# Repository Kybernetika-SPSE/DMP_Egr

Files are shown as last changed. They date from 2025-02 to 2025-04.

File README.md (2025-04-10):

# Stanice pro monitorování okolního prostředí

## Zadání
Cílem práce je navrhnout a vytvořit model pásové linky, která bude využívat robotickou ruku na manipulaci se zásilkami.

## Vedoucí práce
Jiří Švihla

## Harmonogram práce
- [x]   Návrh celého modelu a výběr potřebných součástek (31.10.)
- [x]   Návrh a vytvoření jednotlivých pásů (28.11.)
- [x]   Seznámení se s fungování robotického ramena (19.12.)
- [x]   Vývoj softwaru pro řízení celého modelu (30.1.)
- [x]   Kompletování modelu a následné testovaní (27.2.)
- [x]   Zpracování dokumentace (24. 3.)

## Termín odevzdání
31. března 2025

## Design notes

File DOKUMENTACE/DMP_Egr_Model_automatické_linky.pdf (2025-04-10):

## Vyšší odborná škola

## a Střední průmyslová škola elektrotechnická

## Plzeň, Koterovská 85

DLOUHODOBA MATURITN ´ | Í PRACE ´

## S OBHAJOBOU

### Téma:

# Model automatické linky

Autor práce: | Lukáš Egr
Třída: | 4.L

## Vedoucí práce: Jiří Svihla ˇ

Dne: | 31.3.2025

## Hodnocení:

Vyšší odborná škola
a Střední průmyslová škola elektrotechnická Plzeň, Koterovská 85

# Zadání dlouhodobé maturitní práce

Žák: | Lukáš EGR
Třída: | 4. L

### Studijní obor: 78-42-M/01 Technické lyceum

Zaměření: | bez zaměření
Školní rok: | 2024 - 2025
Téma práce: | Model automatické linky

### Pokyny k obsahu a rozsahu práce:

Cílem práce je navrhnout a vytvořit model pásové linky, která bude využívat robotickou ruku na manipulaci se zásilkami.

1. Návrh celého modelu a výběr potřebných součástek (31.10.) 2. Návrh a vytvoření jednotlivých pásů (28.11.) 3. Seznámení se s fungování robotického ramena (19.12.) 4. Vývoj softwaru pro řízení celého modelu (30.1.) 5. Kompletování modelu a následné testovaní (27.2.) 6. Zpracování dokumentace (24.3.)

Termín odevzdání: | 31. března 2025
Čas obhajoby: | 15 minut
Vedoucí práce: | Jiří Švihla

Projednáno v katedře ODP, a schváleno ředitelem školy.

V Plzni dne: 30. září 2024 | Mgr. Jan Syřínek Zástupce ŘŠ , zástupce statutárního orgánu Vedoucí organizace VOŠ, SŠ, DM

## Anotace

Tato maturitní práce se zabývá návrhem a sestavení modelu automatické třídicí linky,

která simuluje proces třídění příchozích výrobků. Linka se skládá z pásového dopravníku

a robotického ramene, které se stará o manipulaci s výrobky a jejich následné třídění do

určených pozic.

Cílem projektu je vytvořit funkční systém, který umožní automatické rozpoznávání a

třídění výrobků podle definovaných pravidel. Díky tomu můžeme nahlédnout do světa

průmyslové automatizace a její složitosti.

Prohlašuji, že jsem tuto práci vypracoval samostatně a použil literárních pramenů

a informací, které cituji a uvádím v seznamu použité literatury a zdrojů informací.

Prohlašuji, že jsem nástroje UI využil v souladu s principy akademické integrity a že na

využití těchto nástrojů v práci vhodným způsobem odkazuji.

Souhlasím s využitím mé práce učiteli VOS a SP ˇ | SE Plzeň k výuce. ˇ
V Plzni dne 31. 3. 2025 | Podpis: |

## Annotation

This graduation thesis deals with the design and implementation of a model of an auto-

matic sorting line that simulates the process of sorting of incoming products. The line is

composed of a conveyor belt, and a robotic arm that takes care of the manipulation of

products and their subsequent sorting into certain positions.

The aim of the project is to create a functional system that allows automatic recognition

and sorting of products according to defined rules. This will give us an insight into the

world of industrial automation and its complexity.

I declare that I have prepared this thesis independently and have used literature sour-

ces and information, which I cite and list in the list of used literature and sources of

information.

I declare that I have used the UI tools in accordance with the principles of academic

integrity and that I have appropriately referenced the use of these tools in my work.

I agree to the use of my work by the teachers of the Higher School of Education and

Secondary School of Education Pilsen for teaching.

In Pilsen 31. 3. 2025 | Podpis: |

## Obsah

Uvod ´ | 6
1 Hardware | 7
2 Software | 15
3 Závěr | 19
Literatura | 20
Přílohy | 22

## Uvod ´

V dnešní době se stále více firem spoléhá na automatizaci, která jim umožňuje zvýšit

efektivitu a přesnost logistických procesů. Se zvyšujícím se objemem online objednávek

roste i tlak na co nejrychlejší a nejspolehlivější třídění a doručování zásilek.

Automatizované systémy třídění se proto využívají nejen v logistice, ale také v průmyslové

výrobě, kde je potřeba efektivně rozřazovat produkty podle různých kritérií, například

podle barvy, hmotnosti nebo rozměrů. Klíčovou součástí těchto systémů jsou dopravníky,

senzory a robotická ramena, která umožňují manipulaci s objekty a jejich přesné umístění

na požadovaná místa.

### Cíl práce

Cílem této práce je navrhnout a realizovat model automatické třídicí linky, která demon-

struje principy moderních třídicích systémů. Linka bude využívat dopravní pás, senzo-

rický systém a robotickou ruku k rozřazování objektů představujících balíčky či výstupy

z výroby. V rámci projektu bylo nutné nejen navrhnout a sestavit mechanickou konstrukci

linky, ale také vyvinout odpovídající software, který zajistí její správné fungování – od

inicializace, přes detekci objektů, až po jejich přesné umístění do předem definovaných

pozic.

Tento projekt ukazuje, jak lze pomocí kombinace mechanických a elektronických prvků

spolu s programovým řízením vytvořit efektivní třídicí systém, který může sloužit jako

základ pro větší a komplexnější automatizační řešení.

6

## 1 Hardware

Pro realizaci automatické třídicí linky bylo nutné navrhnout a sestavit jednotlivé hardwa-

rové komponenty tak, aby společně tvořily funkční celek. Každá část linky plní specific-

kou úlohu a simuluje tím reálný automatický systém, který dokáže pracovat bez nutnosti

uživatelského zásahu. Klíčovými prvky jsou robotické rameno, které manipuluje s objekty, dopravníkový pás, zajišt’ující jejich přesun a identifikaci, a napájecí systém dodávající

energii všem komponentám.

### 1.1 Rameno

Robotické ramena ruky jsou obvykle, jako i v mém případě, poháněna servomotory, které umožňují přesný a rychlý pohyb. Rídicí signál, který servo přijímá, je často ve formě délky ˇ

impulzu neboli PWM (Pulse Width Modulation). Elektronická deska serva tento signál

přijme a poté měří šířku daného impulsu v čase, která určuje požadovanou polohu motoru (viz. Obrázek 1.1). Motor pak reaguje na tento signál otáčením do určitého úhlu, který

se servo snaží udržet nepřetržitou korekcí polohy [1]. Tímto způsobem lze servo motory

napozicovat podle potřeb do předem definovaných pozic.

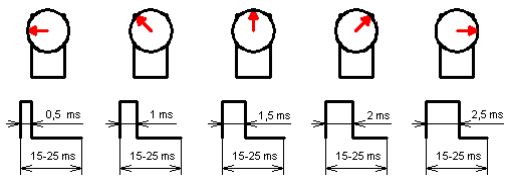
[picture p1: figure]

Obrázek 1.1: Příklady PWM signálu [2]

7

Robotická ruka je vybavena šesti servomotory MG996R, které umožňují pohyb v rozsahu

120 stupňů, tedy 60 stupňů na každou stranu. Tento rozsah otáčení poskytuje dostatečnou

flexibilitu pro manipulaci s objekty v pracovním prostoru ramene. Maximální dosah ruky

činí až 35 cm, což je pro model více něž dostačující.

Základna robotické ruky je konstruována z dvou hliníkových profilů, které zajišt’ují stabilní

uchycení celé konstrukce ramena. Tyto profily jsou upevněny na desku pomocí několika

úhelníků, šroubů M8 a závrtných matic. Díky tomu je garantována vysoká stabilita ro-

botického ramene, což je klíčové pro jeho přesné a spolehlivé fungování.

### 1.2 Dopravníkový pás

Dopravníkový pás je jedna z hlavních prvků modelu třídicí linky, je složen z 3D tištěných

dílů, ložisek, hlazených tyčí, gumového pásu a hliníkových profilů. Právě použití těchto

dílů umožňuje variabilní sestavení pásu. Například je možné veškeré díly jednoduše z kon-

strukce pásu demontovat nebo je naopak na konstrukci přidat.

Díky 3D tisku jsem mohl veškeré modely přizpůsobit pro potřeby jednotlivých komponent

a potřeb celého modelu. Byla brána v potaz, jak velikost součástek, tak i jejich umístění,

myslelo se ale i na množství spotřebovaného materiálu nebo cirkulaci vzduchu, abych

zamezil přehřívání součástek. Veškeré díly jsou do hliníkových profilů umístěny pomocí

šroubů M6 s válcovou hlavou a zajištěny příslušnou maticí.

### Konstrukce dopravníku

Hlavní konstrukce dopravníku je tvořena čtyřmi hliníkovými profily různých délek. Spe-

cificky mají rozměry 30 na 30 mm a délku 400 mm a 40 mm a navzájem jsou spojeny tzv. úhelníky (viz. Obrázek 1.2). Střed konstrukce dopravníkového pásu je vyztužena několika žebry, které zajišt’ují celkovou pevnost celého pásu a zároveň zabraňují prověšení

pásu ve ve středu mezi profily (Přílohy I a II).

Nohy dopravníkového pásu jsou také 3D tištěné (Příloha III). Model jako takový je

8

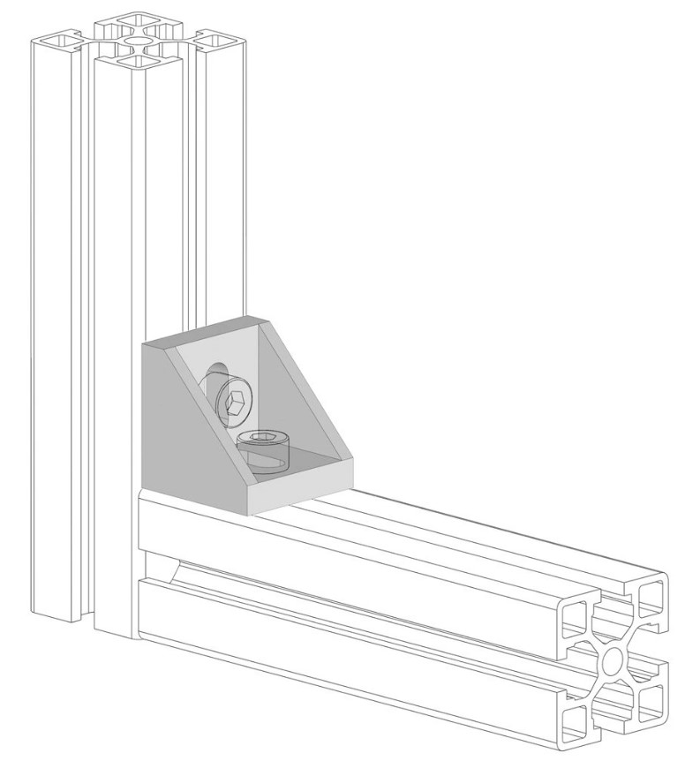
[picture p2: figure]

Obrázek 1.2: Nastínění spojení profilů [3]

navržen tak, aby přesahoval o 2 mm nad plochu profilů. To napomáhá plynulému chodu

gumového pásu, kterému přesah slouží jako ”kolejnice”, do kterých pás plynule zajede.

Zabraňují tedy ve vyklouzávání gumového pásu a udržuje ho ve správné poloze.

### Krokový motor

Gumový pás je poháněn díky krokovému motoru NEMMA 17, který disponuje silou 40 N · cm. Motor je na konstrukci dopravníku upevněn díky tištěnému 3D modelu

(Příloha IV ) a abych co nejvíce eliminoval vibrace, spojené s pohybem motoru, je mezi

model a motor vložena gumová vložka.

Z důvodu velikosti a váze motoru je motor umístěn pod samotným dopravníkem. Točivý

moment motoru je na hlazenou tyč poté převáděn pomocí převodu složeného ze dvou

řemeniček a řemenu.

Abych zvětšil poloměr otáčení, je na hlazené tyči umístěn tištěný válec (Příloha V ). Tyč

je zároveň umístěna do ložisek, která jsou zabudovaná do 3D modelu nohy, pro snížení

odporu, díky čemuž se gumový pás dokáže pohybovat plynuleji. Na koncích profilů jsou rovněž vsazeny záslepky profilů (Příloha VI), jenž zahlazují hrany profilů, tím pádem

9

zabraňují poškození gumového pásu a snižují odpor, který by hrana kladla proti pásu.

Tímto vším také celkově snižuji spotřebu energie, kterou by motor musel pro pohyb

použít.

Krokové motory jako takové, jsou často využívány v robotice a automatizaci pro svou

schopnost přesného pohybu. Na rozdíl od servomotorů, které využívají PWM signál

k určení úhlu natočení, krokové motory pracují na principu sekvenčního napájení jed-

notlivých vinutí statoru.

Rídicí jednotka motoru, v mém případě A4988, která je na dopravník připevněna po- ˇ

mocí krabičky a víčka (Příloha VII a VIII). Ta vysílá sérii elektrických impulzů do

vinutí motoru v přesném pořadí, což způsobuje, že rotor postupně mění svou polohu

po malých úhlových krocích. Počet těchto kroků určuje celkový úhel otočení motoru (viz. Obrázek 1.3).

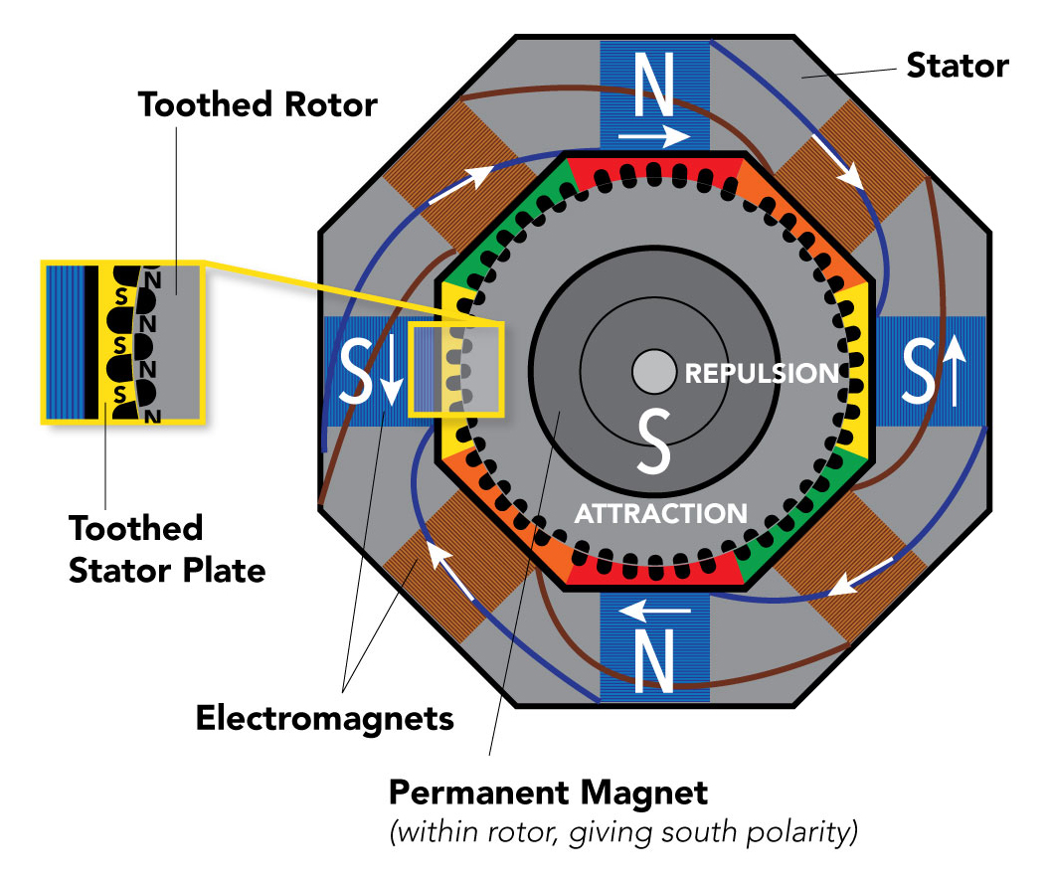
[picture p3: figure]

Obrázek 1.3: Diagram krokového motoru [4]

10

### Senzor barvy

Součástí dopravníku je také portál se senzorem barvy (Přílohy IX a X ), který identifikuje

barvu kostičky, podle čehož se odvíjí další kroky procesu třídění. My využíváme senzor

TCS3200, ten má pole fotodiod se 4 různými filtry:

- 16 fotodiod s červeným filtrem – citlivým na červenou vlnovou délku
- 16 fotodiod se zeleným filtrem – citlivých na zelenou vlnovou délku
- 16 fotodiod s modrým filtrem – citlivým na modrou vlnovou délku
- 16 fotodiod bez filtru

Signál z fotodiod prochází přes převodník, který hodnoty převede na analogový signál s frekvencí. Ta nám určuje intenzitu světla snímané barvy (viz. Obrázek 1.4).

Obrázek 1.4: Diagram převodu signálu [5]

Pro zjištění snímané barvy jednoduše porovnávám jednotlivé hodnoty ze všech filtrů.

Abych získal transparentnější výsledky, rozpoznávám barvy červené, zelené a modré. Roz-

poznávaná barva se tak zpravidla projevuje nízkou hodnotou na konkrétním filtru. Pokud

tedy například přiložíme k senzoru červenou kostku, odražené světlo, které vyzařují bílé

diody na stranách senzoru, bude obsahovat nejvíce červenou barvu, a ta vygeneruje nejvíce proudu skrze fotodiody s červeným filtrem [6].

### IR senzory

IR senzor má na své desce dvě diody. Vysílací diodu, která neustále vysílá infra červené

světlo, a přijímací diodu, jenž kontroluje jestli nějaké nedetekovala. Pokud se tedy před

11 senzor postaví nějaký objekt, odrazí vysílané infra červené světlo zpátky k senzoru a

přijímací dioda ho zaznamená. Po zaznamenání vyšle elektrický signál, který se přes převodník změní na digitální výstup (viz. Obrázek 1.5) [7].

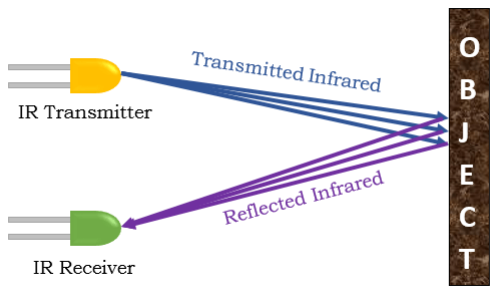
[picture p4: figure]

Obrázek 1.5: Fungování senzoru [8]

Na desce senzoru je také potenciometr, díky kterému můžeme měnit měřící vzdálenost senzoru. A na dopravník je připevněn pomocí držáku (Příloha XI).

### RGB modul a semafor

RGB modul má na desce jednu diodu, ta je ale ve skutečnosti tvořena 3 samostatnými LED

diodami červené, zelené, a modré barvy. Požadovanou barvu poté nastavuji různě silnými

PWM signály na každou z těchto ledek. Výsledná barva je tedy tvořena 3 základními barvy s různými svítivostmi [9].

Semafor funguje podobně jako RGB modul, jen s rozdílem že PWM signály určuji jaká

konkrétní led dioda se má rozsvítit.

Všechny tyto součástí jsou řízeny pomocí Arduino mega, které slouží jako mozek celé linky.

Vysílá potřebné signály a zpracovává přijaté data, podle kterých rozhoduje o dalším dění.
Rídicí deska je schovaná v 3D modelované krabičce ( ˇ | Přílohy XIII a XIV )

12

### 1.3 Napájení

Napájení pro celý model zajišt’uje zdroj LYONZG S-240-24, který poskytuje výstupní

napětí 24 V při 10 A [10]. Většina součástek, ale využívá 5 V logiku. Abych součástky

tedy nepoškodil, musíme výstupní napětí snížit. V mém případě pro to používám step-

down měnič LM2596, který s maximálním vstupním napětím od 3 V do 33 V a výstupním

proudem 24 V, je pro naše potřeby dostačující. Jelikož je ale maximální výstupní proud 2 A, má každý pár součástek svůj vlastní stepdown [11].

Všechny stepdowny jsou umístěny v jedné krabičce, jejíž návrh zohledňuje možné

přehřívání součástky, proto jsou v modelu zahrnuty otvory pro cirkulaci vzduchu. Pro napájení celého modelu využíváme 8 stepdownů (Přílohy XV a XVI).

### Rameno

Robotické rameno využívá servomotory MG966R. Ty pro svůj chod potřebují napětí mezi

4,8 V - 7,2 V s proudem okolo 800 mA. Na jeden stepdwon tedy můžeme zapojit pouze 2 serva s celkovým odběrem 1600 mA [12], abych stepdown nebo serva nepoškodil, ale

zároveň měli motory dostatečnou sílu, použijem napětí 6 V.

### Krokový motor

Krokový motor NEMMA 17 a jeho driver A4988 využívají 2 stepdowny. Samotný krokový

motor totiž potřebuje pro svůj chod 12 V a při práci odebírá okolo 1,7 A podle namáhaní [13]. A4988 potřebuje sice 5V a pouze 0,4 A, ale pro zajištění stabilního napájení má

stepdown vlastní [14] .

13

### 5 V logika a arduino

Zbytek senzorů a arduino, jako například senzor barvy TCS3200 nebo IR senzor překážky,

potřebují 5 V, ale mají minimální odběr proudu. Abych ale zamezil přetížení step-downu,

každé dvě součásti mají svůj vlastní. Malé součástky jako RGB led modul KY-016 a modul semaforu jsou napájeny přímo řídicí deskou (Příloha XVII).

14

## 2 Software

Jako řídicí jednotku jsem zvolil arduino mega, které poskytuje dostatečné množství, at’

už digitálních analogových nebo PWM pinů. Zároveň má také dostatečně velkou pamět’ a

rychlost čtení kódu. Náš kód jako celek je rozdělen na několik hlavních částí. Inicializace,

2 hlavní smyčky a funkce.

### 2.1 Inicializace

V části inicializace se definují piny, na kterých jsou komponenty připojeny. Například na

jakém pinu je vstup z barveného senzoru a na jakém pinu je výstup. A také si definujeme

jaké knihovny budeme v kódu využívat.

V mém případě využívám dvě knihovny. Konkrétně knihovnu pro ovládání servomotorů (Servo.h [15]) a základní knihovnu pro arduino (Arduino.h [16]), abych mohl využívat

časové funkce.

Součástí inicializace je také funkce pro eliminaci zákmitů IR senzoru (tzv. debouncing).

Při práci s IR senzory dochází často k problémům způsobeným krátkodobými změnami

signálu, které mohou vést k falešným detekcím. Tento jev je způsoben například elek-

trickým šumem nebo mechanickými vibracemi. Pro zajištění spolehlivého rozpoznání

stavu senzoru proto využíváme techniku zvanou debouncing, která stabilizuje signál před

jeho dalším zpracováním.

Princip spočívá v opakovaném měření hodnoty signálu v krátkých časových intervalech.

Pokud senzor po několika po sobě jdoucích měřeních stále vykazuje stejný stav, považuje

se jeho výstup za stabilní a lze jej použít k řízení dalších procesů. Tento přístup eliminuje

krátkodobé rušivé signály, které by mohly vést k nesprávným rozhodnutím systému.

Použití této metody zvyšuje spolehlivost detekce objektů a zajišt’uje přesnější vyhodnocení

15 přítomnosti překážek v automatizovaných systémech.

### 2.2 Setup

První hlavní smyčka je tzv. setup cyklus. V této smyčce přiřazuji definovaným pinům,

u každé součástky, jestli se jedná o vstup nebo o výstup. A poté se spustí sériová komuni-

kace mezi součástkami a řídicí jednotkou arduinem. Ta umožňuje přenos dat po jednom

bitu v určitém pořadí a je běžně využívána pro ladění kódu nebo komunikaci s externími zařízeními. Přenosovou rychlost nastavíme na 9600 baudů (baud rate), tedy počet bitů

přenesených za sekundu.

Poté proběhne základní kalibrace celého modelu. Konkrétně se vyzkouší komunikace mezi

motorovým kontrolérem a motorem. Tím zjistíme, jestli motor schopen přijímat signály

z jeho kontroléru, a tedy jestli se motor pohybuje. Poté se vyšlou první PWM signály,

pro každé servo rameno, aby se rameno nastavilo do základní pozice, na kterou navazuje

zbytek kódu.

### 2.3 Hlavní smyčka

V hlavní smyčce kódu pouze přivolávám předdefinované funkce jednotlivých součástí,

jako například funkce spuštění motoru, funkce pro měření barvy nebo funkce pro detekci překážky (viz. Obrázek 2.1).

### 2.4 Funkce

Pro zjednodušení hlavní části kódu, jsou do této části volané pouze funkce, které repre-

zentují bloky kódu, pro ovládání konkrétních součástí.

Například funkce pro ovládání ramena počítá rozdíl mezi koncovou a aktuální pozicí.

Tento rozdíl rozdělí na určitý počet kroků, kterými rameno postupně prochází, než se

dostane do požadované pozice. My tedy do naší definované funkce vkládáme pouze pole

16

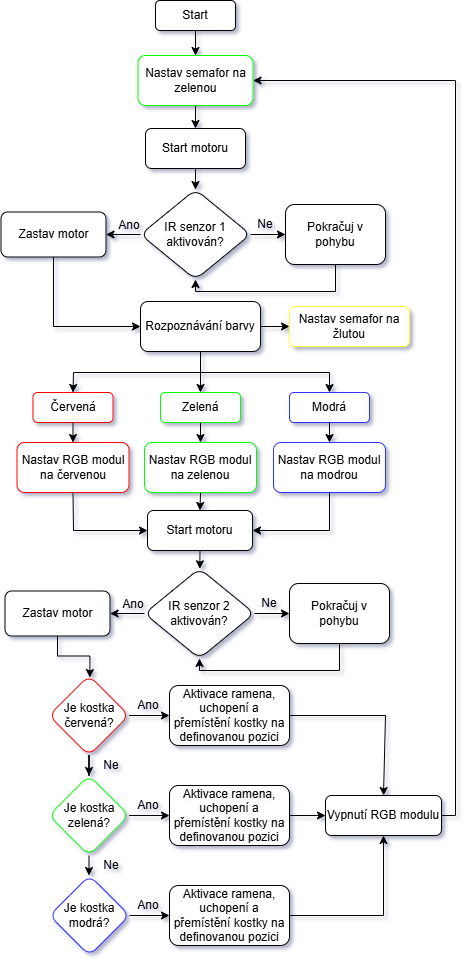
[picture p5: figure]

Obrázek 2.1: Diagram halvního kódu [Zdroj: vlastní, vytvořeno pomocí draw.io]

17 hodnot s úhly, do kterých se má každé servo natočit.

Pohyb ramena je pak určen pouze několika poli hodnot, které definují cestu mezi bodem

A a B skrz několik kontrolních bodů.

Funkce pro měření barvy provede x pokusů pro rozeznání barvy, pokud se tak nestane,

”označí”kostku jako neznámou a podle toho se odvíjí další kroky třídění, tím zabraňujeme

zacyklení programu a jeho následnou nefunkčnost.

18

## 3 Závěr

V rámci této maturitní práce jsem se zaměřil na návrh a kompletaci modelu třídicí linky,

která se skládá z mechanických a elektrických součástí a softwarové část. Celkový systém

byl navržen tak, aby efektivně řídil pohyb gumového pásu pomocí krokového motoru

NEMMA 17, přičemž byla věnována zvláštní pozornost na eliminaci vibrací a zajištění

plynulého chodu.

Senzory, jako například senzor barvy TCS3200 a IR senzory, umožnily precizní detekci

a rozpoznávání kostek, což představovalo klíčový aspekt pro správnou funkci třídícího

procesu. Ošetření hardwarových nedostatků, například u IR senzoru jsem zabránil pomocí

techniky debouncing, která zajistila stabilitu a přesnost měření hodnoty na senzoru.

V softwarové části byl vytvořen modulární kód s využitím Arduina Mega, který umožňuje

snadnou správu jednotlivých funkcí, jako je ovládání motoru, řízení servomotorů pro ro-

botické rameno a ovládaní senzoru barvy nebo IR senzorů.

Celkově tato práce demonstruje úspěšný vhled do mechanických, elektronických a softwa-

rových řešení, se kterými bychom se ve větším měřítku setkali při reálné stavbě automa-

tizovaného systému. Projekt zároveň otevírá možnosti pro další rozšíření a optimalizaci,

jako je to u reálných automatizovaných systémů.

19

## Literatura

[1] JAMECO ELECTRONICS. How Servo Motors Work. [online]. Dostupné z: https://

www.jameco.com/Jameco/workshop/Howitworks/how-servo-motors-work.html

[2] ELECTRONICS | STACK | EXCHANGE. | How | to | get | the | PWM
frequency | and | duration | of | each | pulse. | [online]. | Dostupné | z:

https://electronics.stackexchange.com/questions/129961/

how-to-get-the-pwm-frequency-and-duration-of-each-pulse (https://electronics.stackexchange.com/questions/129961/how-to-get-the-pwm-frequency-and-duration-of-each-pulse)

[3] VSK PROFILY. Uhelník 90 ´ | ° 38×38 M8. [online]. Dostupné z: https://www.

vsk-profily.cz/uhelnik-90-38x38-m8/

[4] CLIPPARD. | How | Stepper | Motors | Provide | Precision | Cont-
rol. | [online]. | Dostupné | z: | https://www.clippard.com/cms/wiki/

how-stepper-motors-provide-precision-control (https://www.clippard.com/cms/wiki/how-stepper-motors-provide-precision-control)

[5] RANDOM | NERD | TUTORIALS. | Arduino | Color | Sensor | TCS230
TCS3200. | [online]. | Dostupné | z: | https://randomnerdtutorials.com/

arduino-color-sensor-tcs230-tcs3200/ (https://randomnerdtutorials.com/arduino-color-sensor-tcs230-tcs3200/)

[6] DRATEK.CZ. ´ | Arduino detektor barvy. [online]. Dostupné z: https://navody.

dratek.cz/navody-k-produktum/arduino-detektor-barvy.html (https://navody.dratek.cz/navody-k-produktum/arduino-detektor-barvy.html)

[7] DRATEK.CZ. ´ | Infračervený optický senzor. [online]. Dostupné z: https://navody.

dratek.cz/navody-k-produktum/infracerveny-opticky-senzor.html (https://navody.dratek.cz/navody-k-produktum/infracerveny-opticky-senzor.html)

[8] VAYUYAAN. IR Sensor Working. [online]. Dostupné z: https://vayuyaan.com/

blog/ir-sensor-working/ (https://vayuyaan.com/blog/ir-sensor-working/)

[9] DRATEK.CZ. ´ | RGB LED modul KY-016. [online]. Dostupné z: https://navody.

dratek.cz/navody-k-produktum/rgb-led-modul-ky-016.html (https://navody.dratek.cz/navody-k-produktum/rgb-led-modul-ky-016.html)

20

[10] LYONZG. | S-240-12 | Modulový | napájecí | 230V | AC/DC | zdroj | 12V
20A | 240W. | [online]. | Dostupné | z: | https://www.laskakit.cz/

lyonzg-s-240-12-modulovy-napajeci-230v-ac-dc-zdroj-12v-20a-240w/ (https://www.laskakit.cz/lyonzg-s-240-12-modulovy-napajeci-230v-ac-dc-zdroj-12v-20a-240w/)

[11] TEXAS INSTRUMENTS. LM2596 Datasheet. [online]. Dostupné z: https://www.

laskakit.cz/user/related_files/lm2596_datasheet.pdf

[12] TOWER PRO. MG996 Servo Datasheet. [online]. Dostupné z: https://www.

laskakit.cz/user/related_files/mg996.pdf

[13] MOTIONKING. 17HSxxxx Stepper Motor Datasheet. [online]. Dostupné z: https:

//www.laskakit.cz/user/related_files/17hsxxxx-motionking.pdf

[14] DRATEK.CZ. ´ | Dokumentace k produktu. [online]. Dostupné z: https://dratek.cz/

docs/produkty/1/1650/1449880500.pdf (https://dratek.cz/docs/produkty/1/1650/1449880500.pdf)

[15] ARDUINO. Servo Library. [online]. Dostupné z: https://www.arduino.cc/en/

reference/servo (https://www.arduino.cc/en/reference/servo)

[16] ARDUINO. Arduino Core Library. [online]. Dostupné z: https://www.arduino.cc/

reference/en/ (https://www.arduino.cc/reference/en/)

21

## Přílohy

PRˇÍLOHA I Uhelník ´

PRˇÍLOHA II Zebro ˇ

PRˇÍLOHA III Noha dopravníku

PRˇÍLOHA IV Držák motoru

PRˇÍLOHA V Válec

PRˇÍLOHA VI Záslepka

PRˇÍLOHA VII Krabička na A4988

PRˇÍLOHA VIII Víko A4988

PRˇÍLOHA IX Portál senzoru barvy

PRˇÍLOHA X Víko portálu

PRˇÍLOHA XI Držák IR senzoru

PRˇÍLOHA XII Box arduino

PRˇÍLOHA XIII Víko arduina

PRˇÍLOHA XIV Srovnávač

PRˇÍLOHA XV LM2596 box víko

PRˇÍLOHA XVI LM2596 box

PRˇÍLOHA XVII Zapojení maturitní práce

22

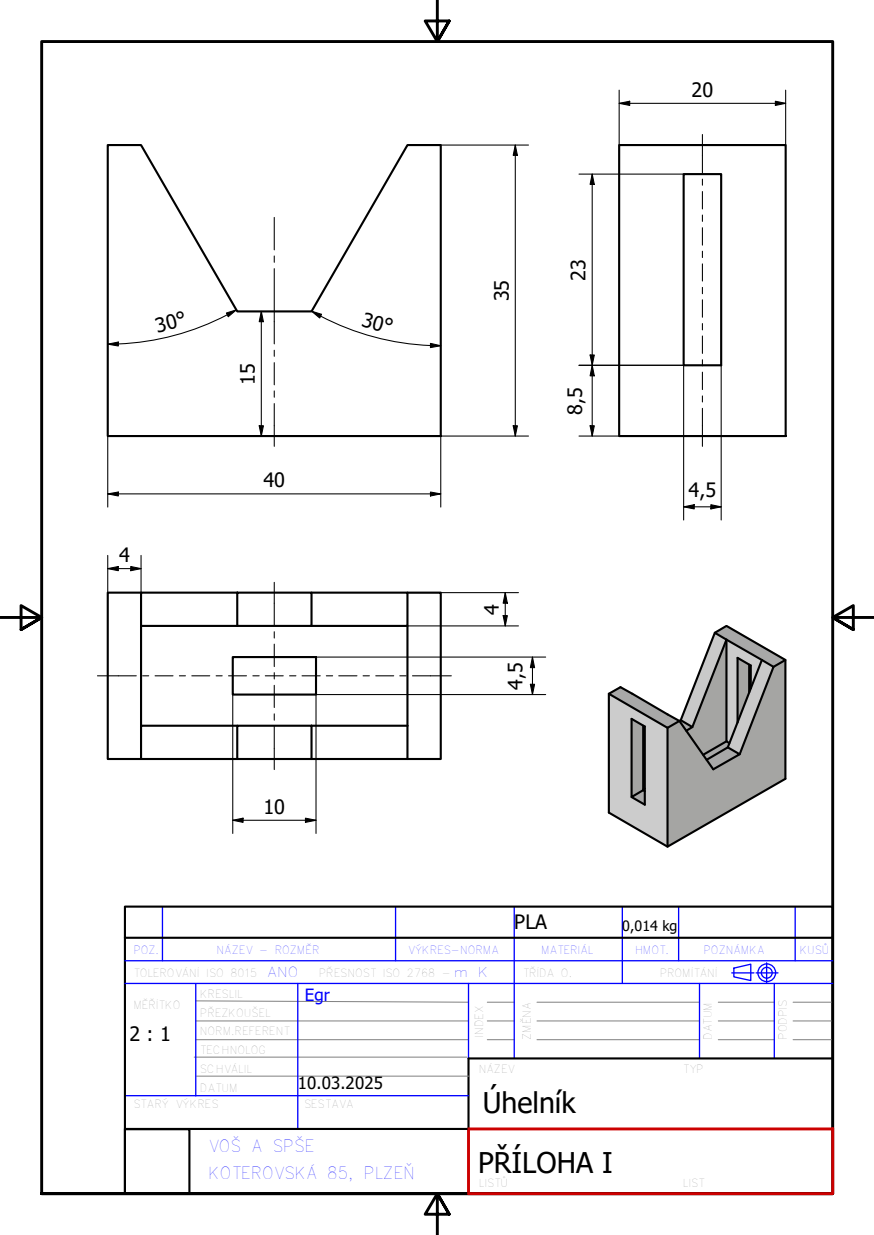
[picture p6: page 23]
VÝKRES-NORMA; POZ.; VOŠ A SPŠE; KOTEROVSKÁ 85, PLZEŇ; NÁZEV - ROZMĚR; POZNÁMKA; ZMĚNA; INDEX; LISTŮ; MATERIÁL; DATUM; LIST; HMOT.; PODPIS; KUSŮ; PLA; PŘÍLOHA I

TOLEROVÁNÍ ISO 8015 ANO PŘESNOST ISO 2768 -m K | TŘÍDA O. | PROMÍTÁNÍ

MĚŘÍTKO 2 : 1 | KRESLIL | Egr

PŘEZKOUŠEL

NORM.REFERENT
TECHNOLOG
SCHVÁLIL | | NÁZEV TYP Úhelník
DATUM | 10.03.2025

STARÝ VÝKRES | | SESTAVA

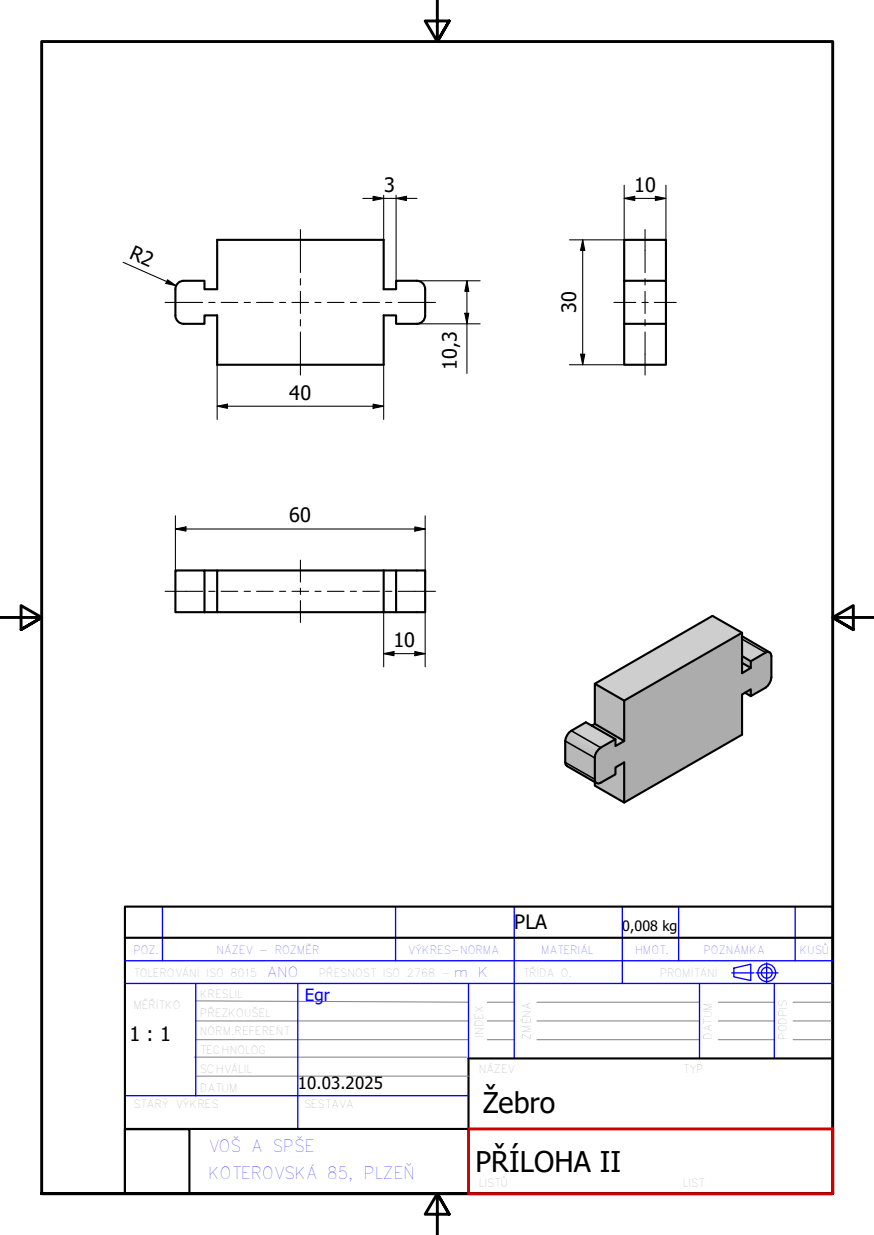
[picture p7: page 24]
VÝKRES-NORMA; POZ.; NÁZEV - ROZMĚR; POZNÁMKA; ZMĚNA; INDEX; MATERIÁL; DATUM; HMOT.; PODPIS; KUSŮ; PLA; PŘÍLOHA II

TOLEROVÁNÍ ISO 8015 ANO PŘESNOST ISO 2768 -m K | TŘÍDA O. | PROMÍTÁNÍ

MĚŘÍTKO 1 : 1 | KRESLIL | Egr

PŘEZKOUŠEL

NORM.REFERENT
TECHNOLOG
SCHVÁLIL | | NÁZEV TYP Žebro
DATUM | 10.03.2025

STARÝ VÝKRES | | SESTAVA

B ( 1 : 1 )
B-B ( 1 : 1 ) | C ( 1 : 1 )

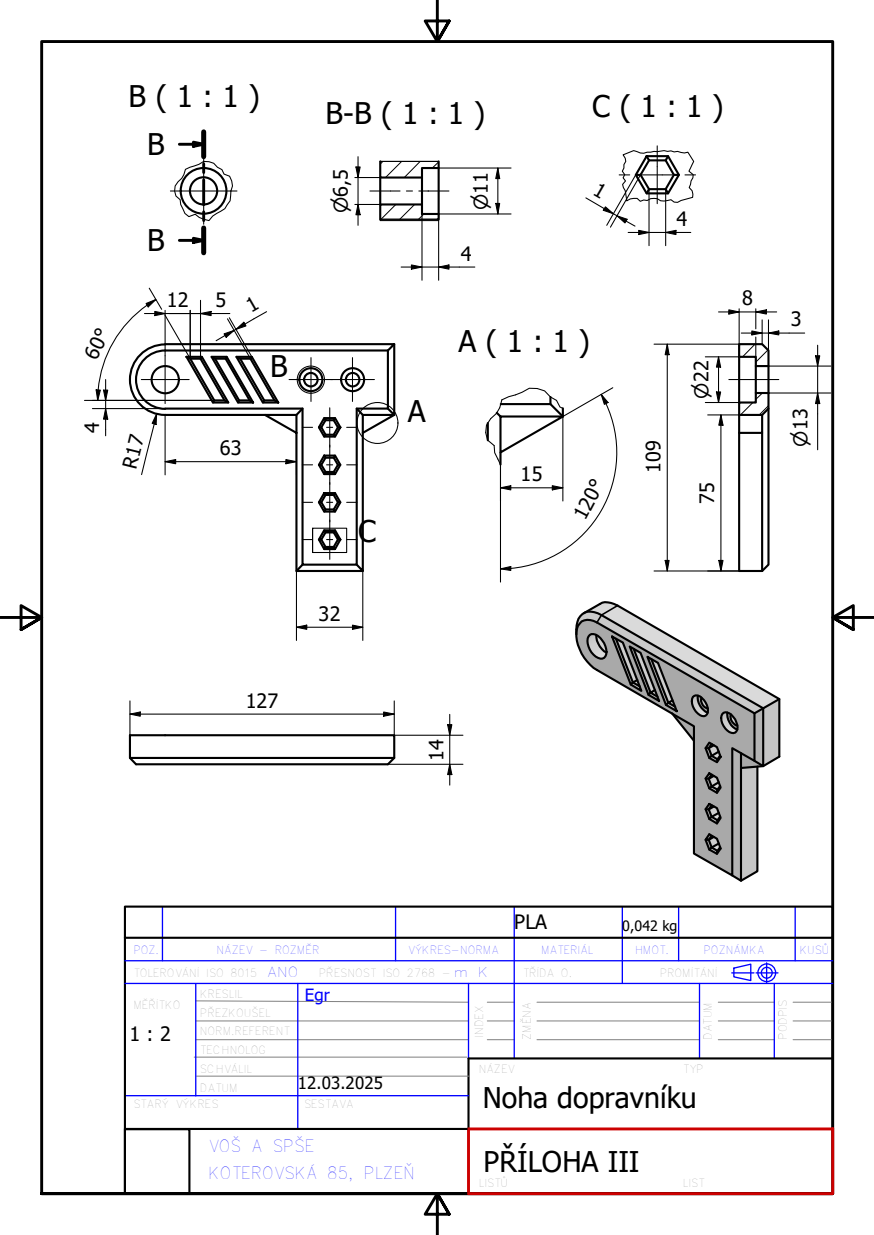
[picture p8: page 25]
VÝKRES-NORMA; POZ.; NÁZEV - ROZMĚR; POZNÁMKA; ZMĚNA; INDEX; MATERIÁL; DATUM; HMOT.; PODPIS; KUSŮ; PLA; PŘÍLOHA III

TOLEROVÁNÍ ISO 8015 ANO PŘESNOST ISO 2768 -m K | TŘÍDA O. | PROMÍTÁNÍ

MĚŘÍTKO 1 : 2 | KRESLIL | Egr

PŘEZKOUŠEL

NORM.REFERENT
TECHNOLOG
SCHVÁLIL | | NÁZEV TYP Noha dopravníku
DATUM | 12.03.2025

STARÝ VÝKRES | | SESTAVA

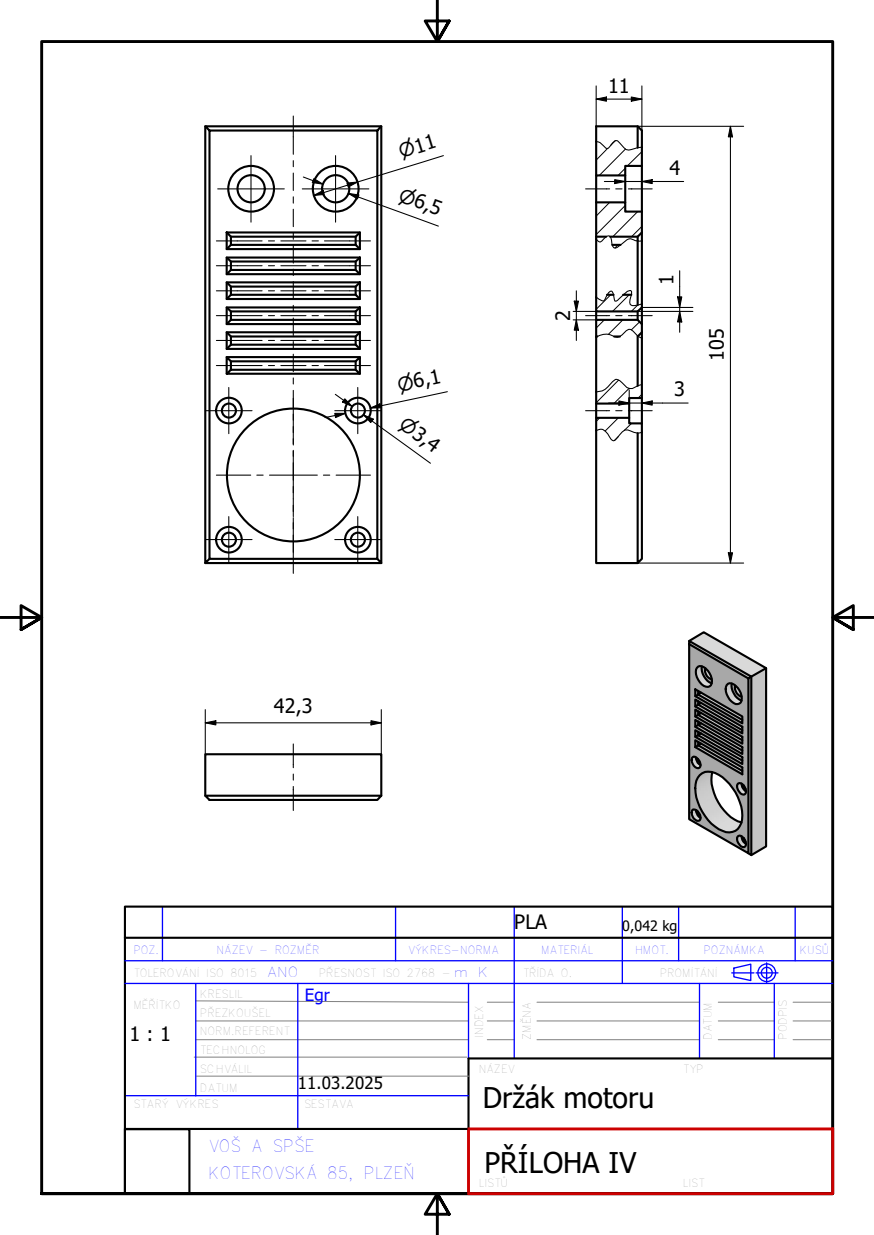
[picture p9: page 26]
VÝKRES-NORMA; POZ.; NÁZEV - ROZMĚR; POZNÁMKA; ZMĚNA; INDEX; MATERIÁL; DATUM; HMOT.; PODPIS; KUSŮ; PLA; PŘÍLOHA IV

TOLEROVÁNÍ ISO 8015 ANO PŘESNOST ISO 2768 -m K | TŘÍDA O. | PROMÍTÁNÍ

MĚŘÍTKO 1 : 1 | KRESLIL | Egr

PŘEZKOUŠEL

NORM.REFERENT
TECHNOLOG
SCHVÁLIL | | NÁZEV TYP Držák motoru
DATUM | 11.03.2025

STARÝ VÝKRES | | SESTAVA

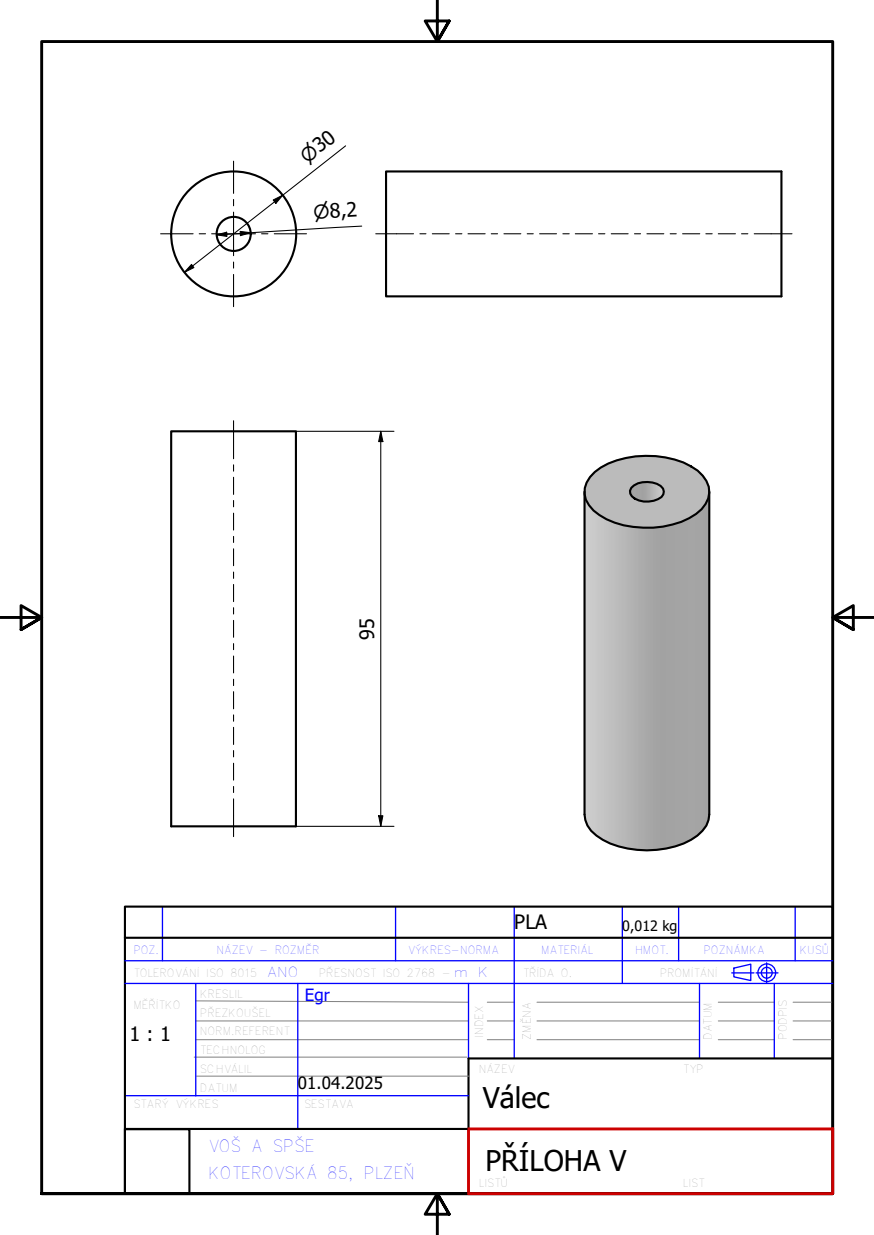
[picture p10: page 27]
VÝKRES-NORMA; POZ.; NÁZEV - ROZMĚR; POZNÁMKA; ZMĚNA; INDEX; MATERIÁL; DATUM; HMOT.; PODPIS; KUSŮ; PLA; PŘÍLOHA V

TOLEROVÁNÍ ISO 8015 ANO PŘESNOST ISO 2768 -m K | TŘÍDA O. | PROMÍTÁNÍ

MĚŘÍTKO 1 : 1 | KRESLIL | Egr

PŘEZKOUŠEL

NORM.REFERENT
TECHNOLOG
SCHVÁLIL | | NÁZEV TYP Válec
DATUM | 01.04.2025

STARÝ VÝKRES | | SESTAVA

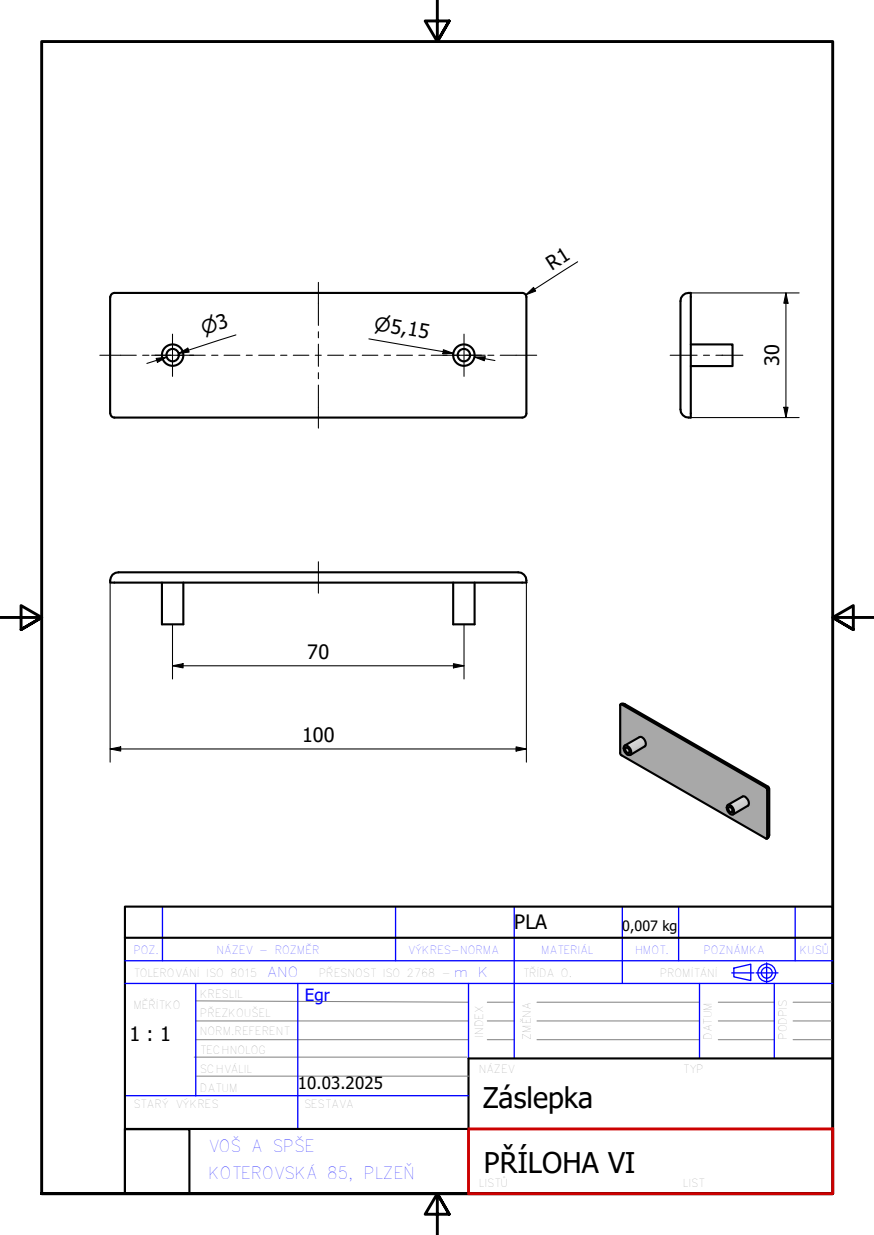
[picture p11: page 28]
VÝKRES-NORMA; POZ.; NÁZEV - ROZMĚR; POZNÁMKA; ZMĚNA; INDEX; MATERIÁL; DATUM; HMOT.; PODPIS; KUSŮ; PLA; PŘÍLOHA VI

TOLEROVÁNÍ ISO 8015 ANO PŘESNOST ISO 2768 -m K | TŘÍDA O. | PROMÍTÁNÍ

MĚŘÍTKO 1 : 1 | KRESLIL | Egr

PŘEZKOUŠEL

NORM.REFERENT
TECHNOLOG
SCHVÁLIL | | NÁZEV TYP Záslepka
DATUM | 10.03.2025

STARÝ VÝKRES | | SESTAVA

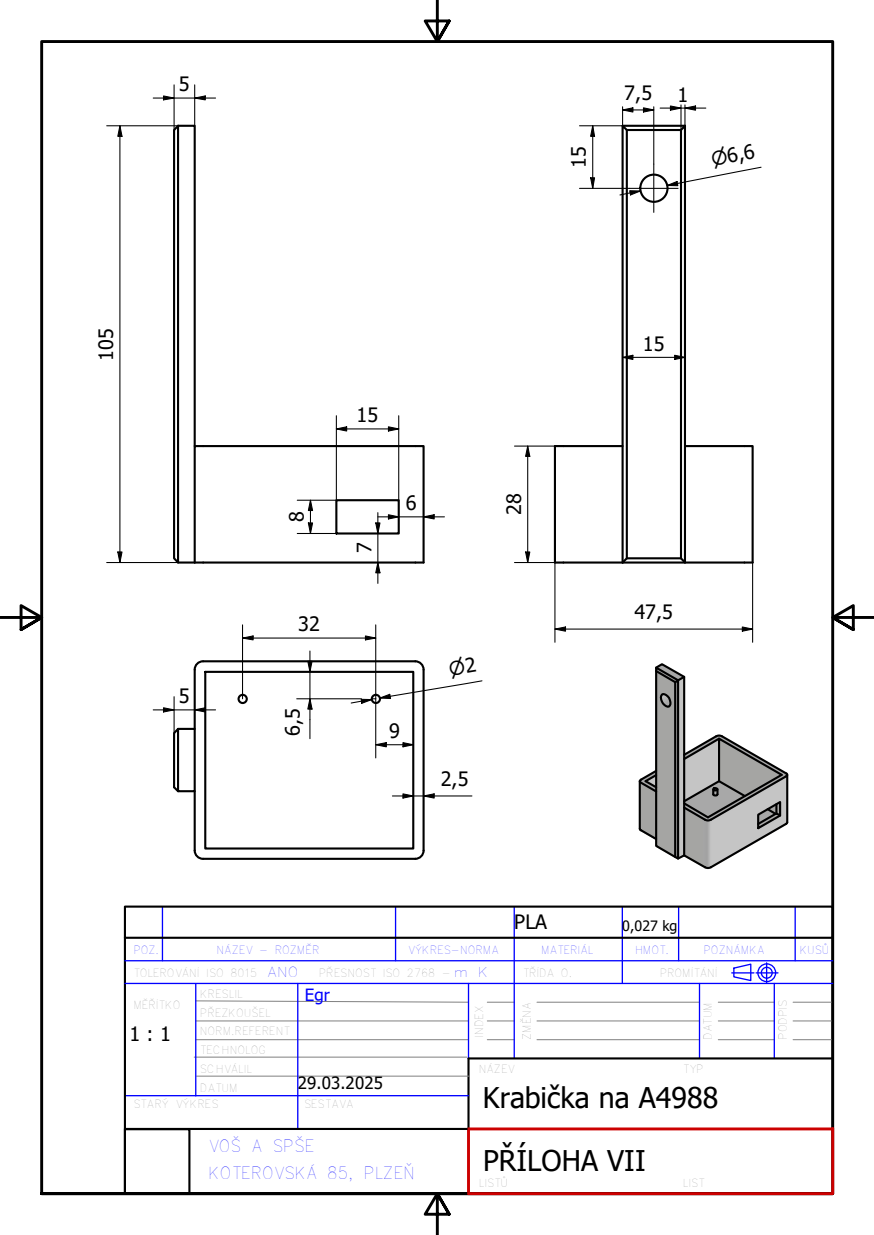
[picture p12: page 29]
VÝKRES-NORMA; POZ.; NÁZEV - ROZMĚR; POZNÁMKA; ZMĚNA; INDEX; MATERIÁL; DATUM; HMOT.; PODPIS; KUSŮ; PLA; PŘÍLOHA VII

TOLEROVÁNÍ ISO 8015 ANO PŘESNOST ISO 2768 -m K | TŘÍDA O. | PROMÍTÁNÍ

MĚŘÍTKO 1 : 1 | KRESLIL | Egr

PŘEZKOUŠEL

NORM.REFERENT
TECHNOLOG
SCHVÁLIL | | NÁZEV TYP Krabička na A4988
DATUM | 29.03.2025

STARÝ VÝKRES | | SESTAVA

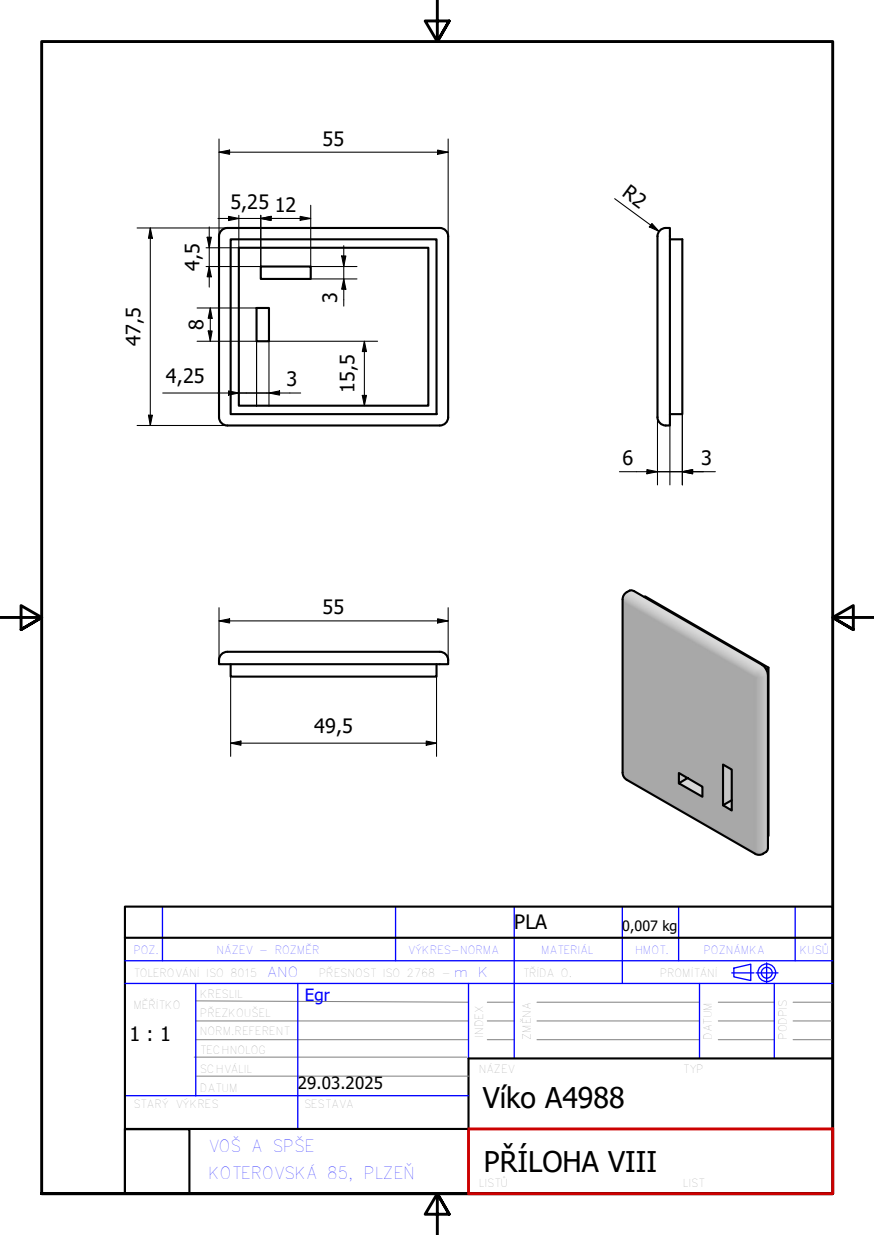
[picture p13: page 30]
VÝKRES-NORMA; POZ.; NÁZEV - ROZMĚR; POZNÁMKA; ZMĚNA; INDEX; MATERIÁL; DATUM; HMOT.; PODPIS; KUSŮ; PLA; PŘÍLOHA VIII

TOLEROVÁNÍ ISO 8015 ANO PŘESNOST ISO 2768 -m K | TŘÍDA O. | PROMÍTÁNÍ

MĚŘÍTKO 1 : 1 | KRESLIL | Egr

PŘEZKOUŠEL

NORM.REFERENT
TECHNOLOG
SCHVÁLIL | | NÁZEV TYP Víko A4988
DATUM | 29.03.2025

STARÝ VÝKRES | | SESTAVA

A

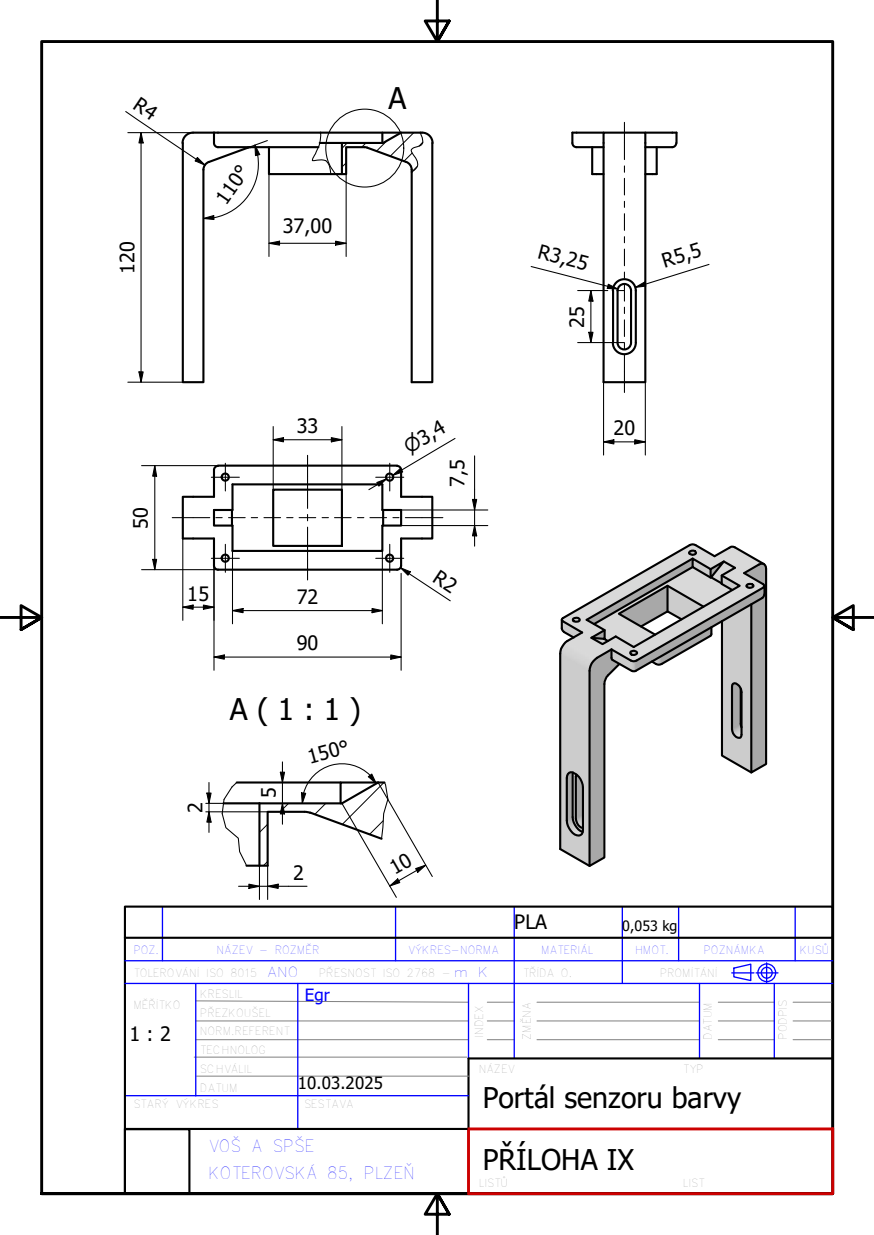
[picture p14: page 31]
VÝKRES-NORMA; POZ.; NÁZEV - ROZMĚR; POZNÁMKA; ZMĚNA; INDEX; MATERIÁL; DATUM; HMOT.; PODPIS; KUSŮ; PLA; PŘÍLOHA IX

TOLEROVÁNÍ ISO 8015 ANO PŘESNOST ISO 2768 -m K | TŘÍDA O. | PROMÍTÁNÍ

MĚŘÍTKO 1 : 2 | KRESLIL | Egr

PŘEZKOUŠEL

NORM.REFERENT
TECHNOLOG
SCHVÁLIL | | NÁZEV TYP Portál senzoru barvy
DATUM | 10.03.2025

STARÝ VÝKRES | | SESTAVA

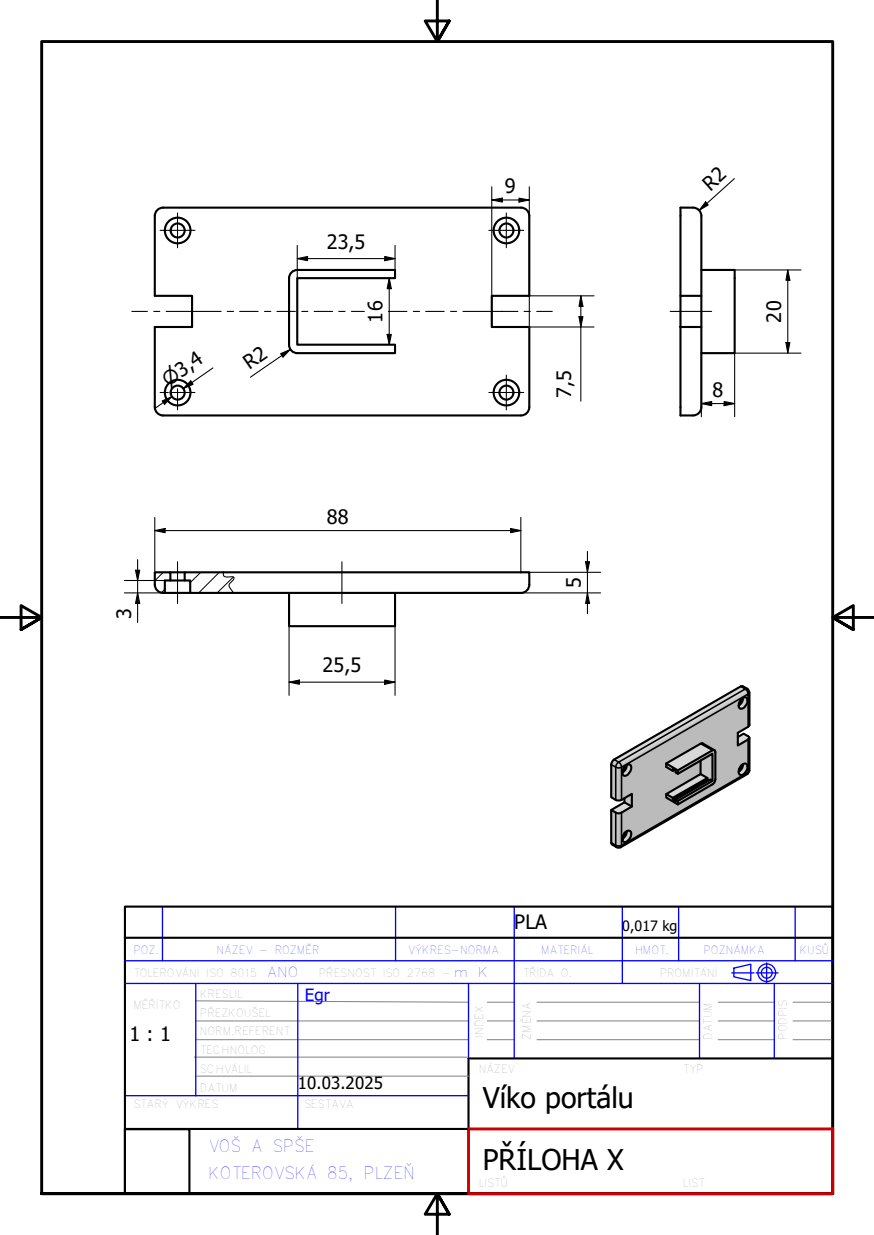
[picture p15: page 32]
VÝKRES-NORMA; POZ.; NÁZEV - ROZMĚR; POZNÁMKA; ZMĚNA; INDEX; MATERIÁL; DATUM; HMOT.; PODPIS; KUSŮ; PLA; PŘÍLOHA X

TOLEROVÁNÍ ISO 8015 ANO PŘESNOST ISO 2768 -m K | TŘÍDA O. | PROMÍTÁNÍ

MĚŘÍTKO 1 : 1 | KRESLIL | Egr

PŘEZKOUŠEL

NORM.REFERENT
TECHNOLOG
SCHVÁLIL | | NÁZEV TYP Víko portálu
DATUM | 10.03.2025

STARÝ VÝKRES | | SESTAVA

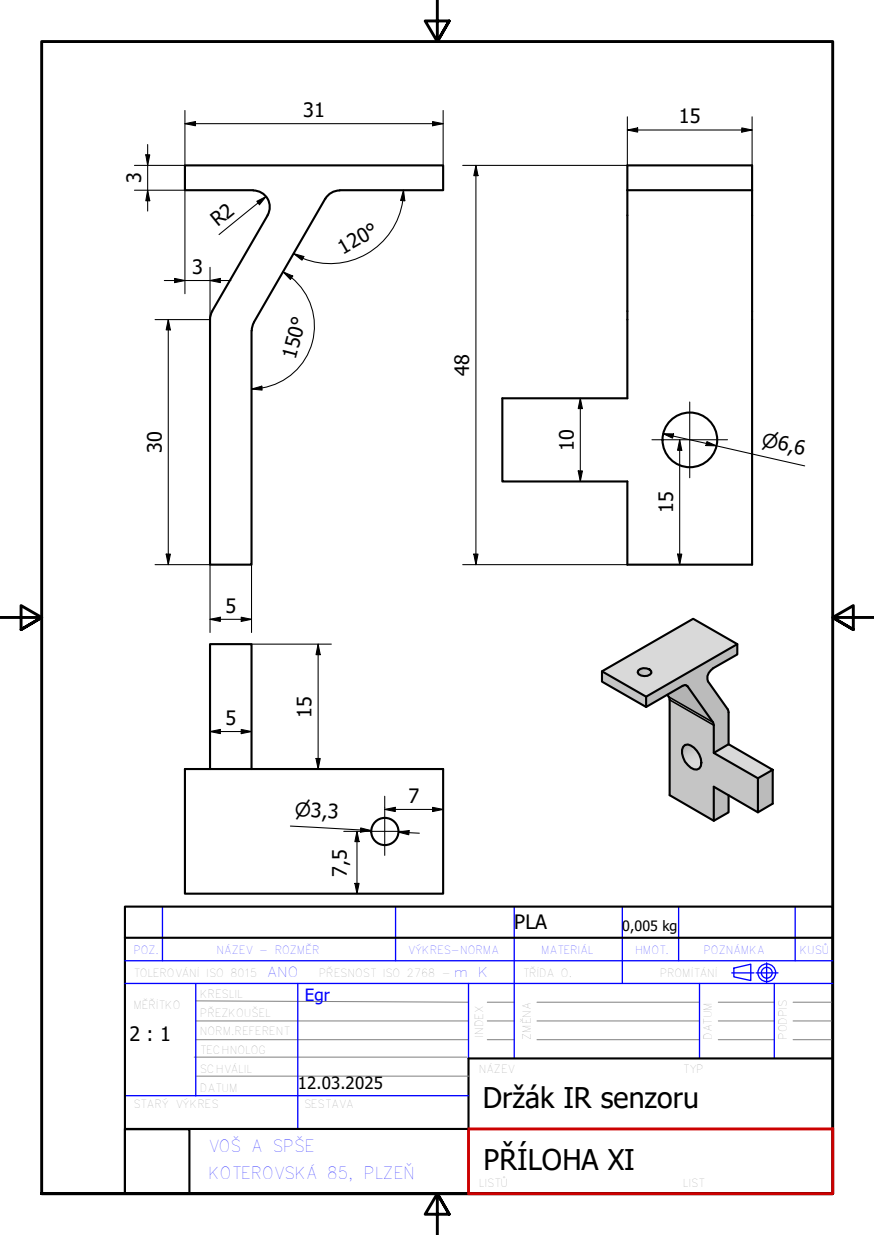
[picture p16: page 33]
VÝKRES-NORMA; POZ.; NÁZEV - ROZMĚR; POZNÁMKA; ZMĚNA; INDEX; MATERIÁL; DATUM; HMOT.; PODPIS; KUSŮ; PLA; PŘÍLOHA XI

TOLEROVÁNÍ ISO 8015 ANO PŘESNOST ISO 2768 -m K | TŘÍDA O. | PROMÍTÁNÍ

MĚŘÍTKO 2 : 1 | KRESLIL | Egr

PŘEZKOUŠEL

NORM.REFERENT
TECHNOLOG
SCHVÁLIL | | NÁZEV TYP Držák IR senzoru
DATUM | 12.03.2025

STARÝ VÝKRES | | SESTAVA

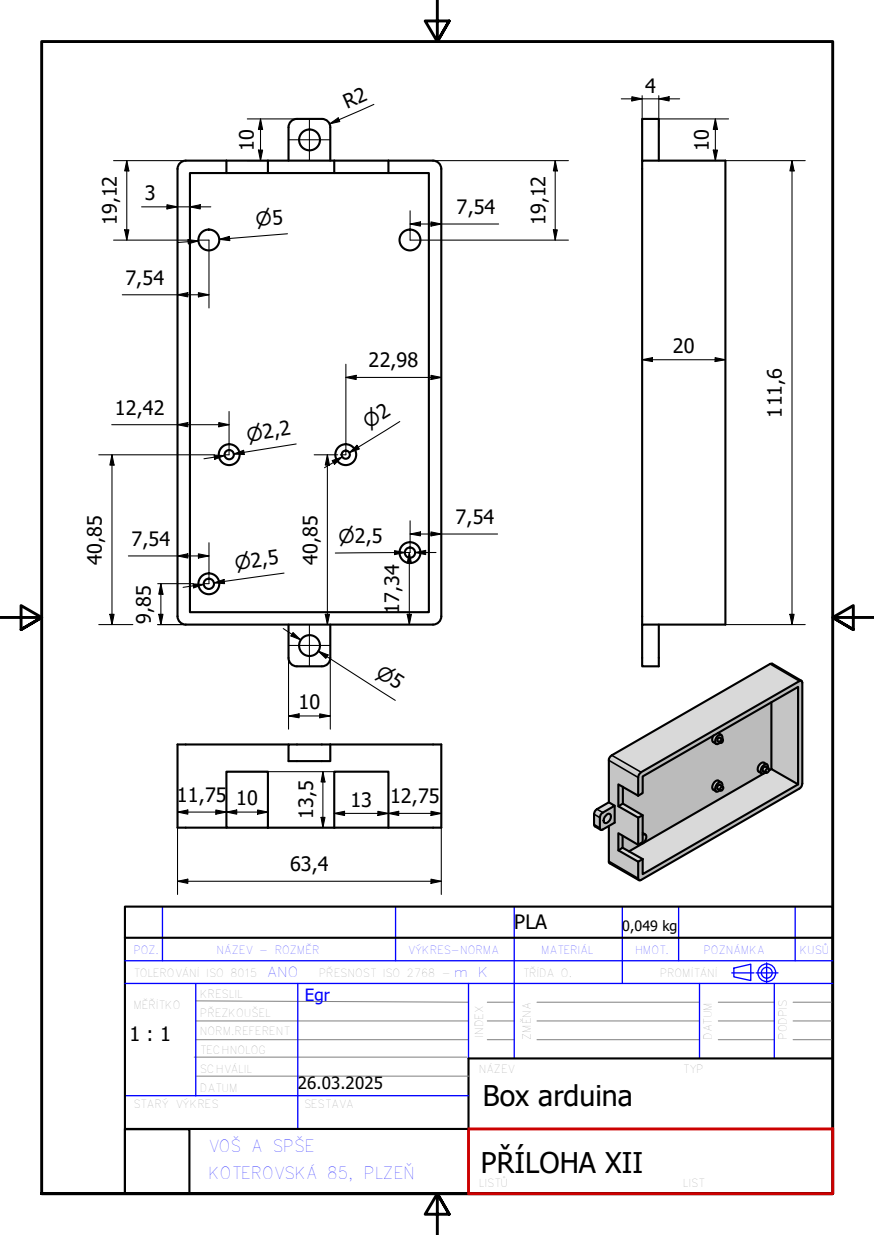
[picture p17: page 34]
VÝKRES-NORMA; POZ.; NÁZEV - ROZMĚR; POZNÁMKA; ZMĚNA; INDEX; MATERIÁL; DATUM; HMOT.; PODPIS; KUSŮ; PLA; PŘÍLOHA XII

TOLEROVÁNÍ ISO 8015 ANO PŘESNOST ISO 2768 -m K | TŘÍDA O. | PROMÍTÁNÍ

MĚŘÍTKO 1 : 1 | KRESLIL | Egr

PŘEZKOUŠEL

NORM.REFERENT
TECHNOLOG
SCHVÁLIL | | NÁZEV TYP Box arduina
DATUM | 26.03.2025

STARÝ VÝKRES | | SESTAVA

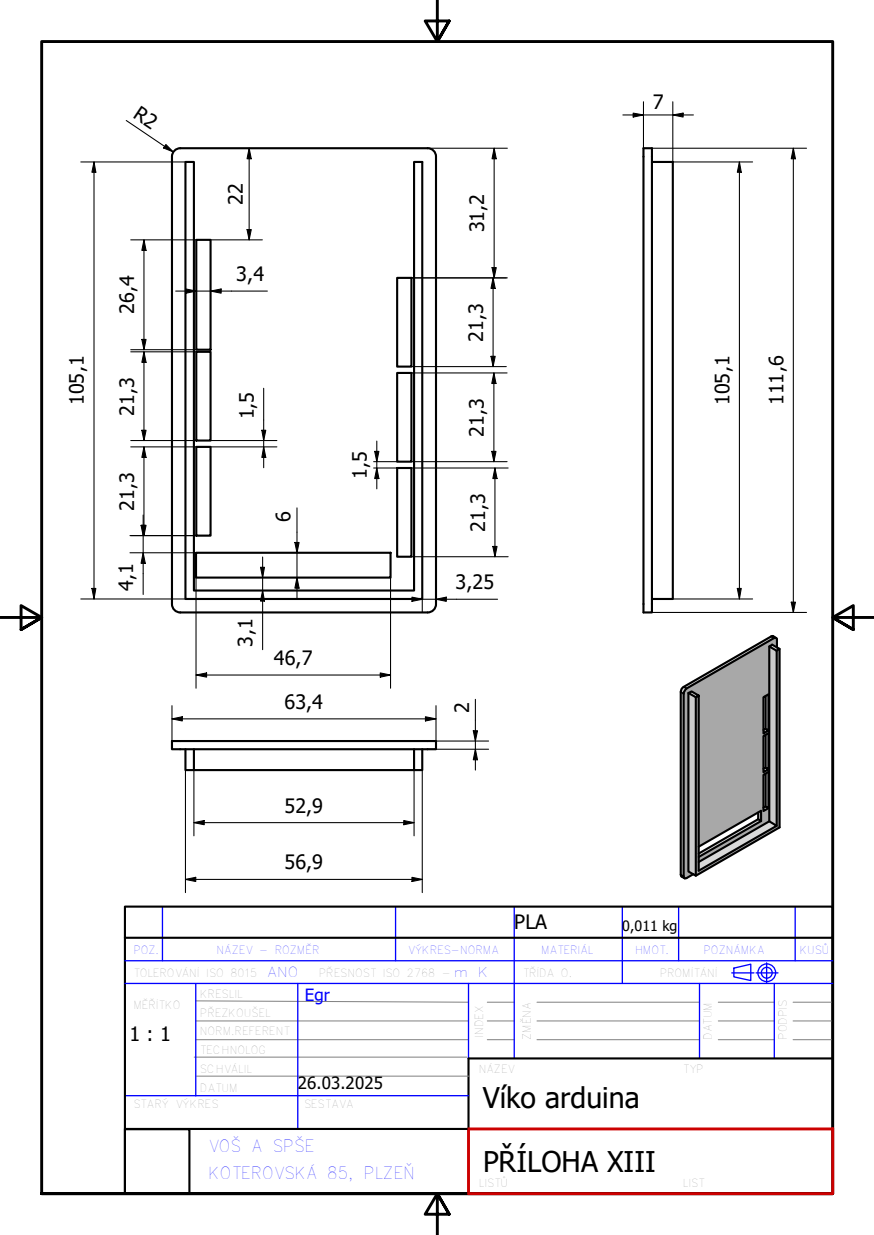
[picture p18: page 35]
VÝKRES-NORMA; POZ.; NÁZEV - ROZMĚR; POZNÁMKA; ZMĚNA; INDEX; MATERIÁL; DATUM; HMOT.; PODPIS; KUSŮ; PLA; PŘÍLOHA XIII

TOLEROVÁNÍ ISO 8015 ANO PŘESNOST ISO 2768 -m K | TŘÍDA O. | PROMÍTÁNÍ

MĚŘÍTKO 1 : 1 | KRESLIL | Egr

PŘEZKOUŠEL

NORM.REFERENT
TECHNOLOG
SCHVÁLIL | | NÁZEV TYP Víko arduina
DATUM | 26.03.2025

STARÝ VÝKRES | | SESTAVA

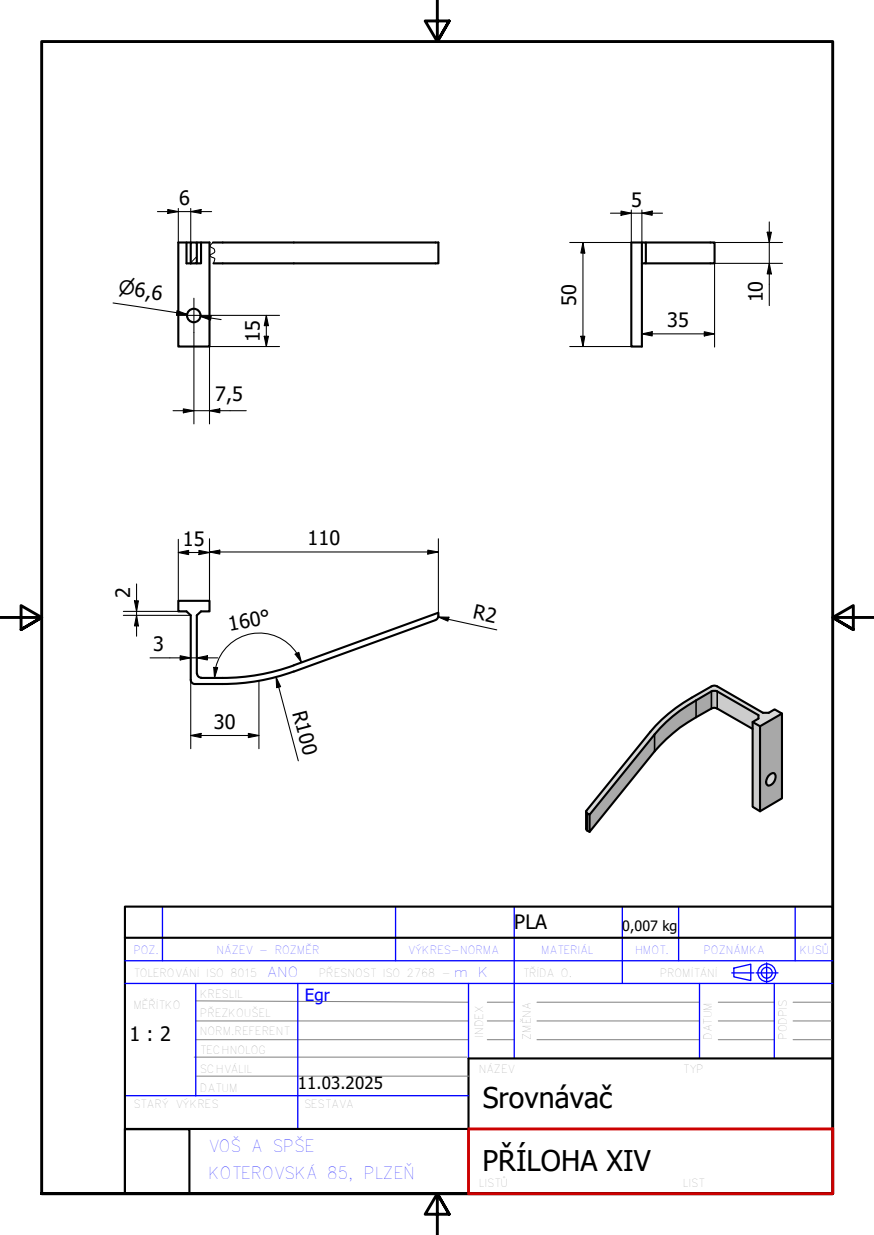
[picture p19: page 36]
VÝKRES-NORMA; POZ.; NÁZEV - ROZMĚR; POZNÁMKA; ZMĚNA; INDEX; MATERIÁL; DATUM; HMOT.; PODPIS; KUSŮ; PLA; PŘÍLOHA XIV

TOLEROVÁNÍ ISO 8015 ANO PŘESNOST ISO 2768 -m K | TŘÍDA O. | PROMÍTÁNÍ

MĚŘÍTKO 1 : 2 | KRESLIL | Egr

PŘEZKOUŠEL

NORM.REFERENT
TECHNOLOG
SCHVÁLIL | | NÁZEV TYP Srovnávač
DATUM | 11.03.2025

STARÝ VÝKRES | | SESTAVA

A ( 1 : 1 )

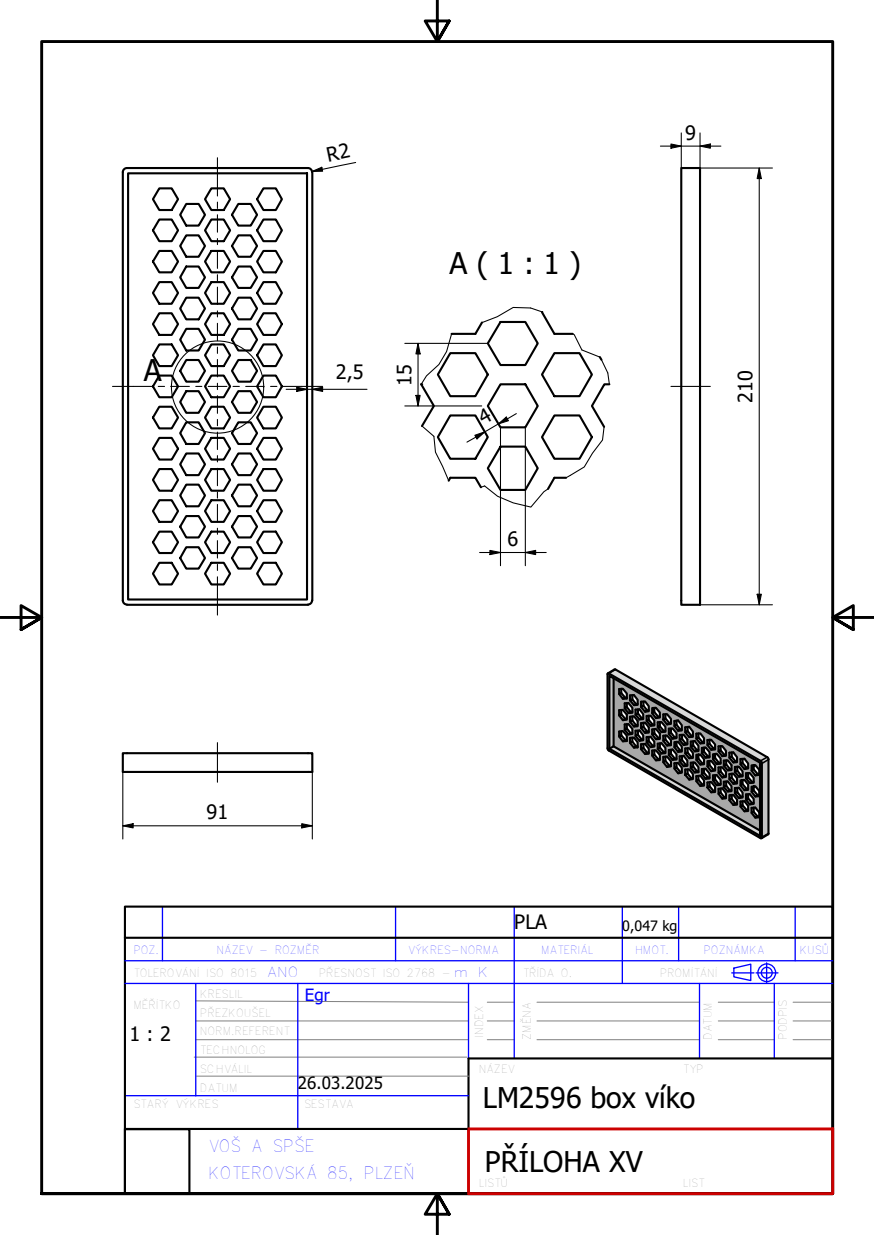
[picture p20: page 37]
VÝKRES-NORMA; POZ.; NÁZEV - ROZMĚR; POZNÁMKA; ZMĚNA; INDEX; MATERIÁL; DATUM; HMOT.; PODPIS; KUSŮ; PLA; PŘÍLOHA XV

TOLEROVÁNÍ ISO 8015 ANO PŘESNOST ISO 2768 -m K | TŘÍDA O. | PROMÍTÁNÍ

MĚŘÍTKO 1 : 2 | KRESLIL | Egr

PŘEZKOUŠEL

NORM.REFERENT
TECHNOLOG
SCHVÁLIL | | NÁZEV TYP LM2596 box víko
DATUM | 26.03.2025

STARÝ VÝKRES | | SESTAVA

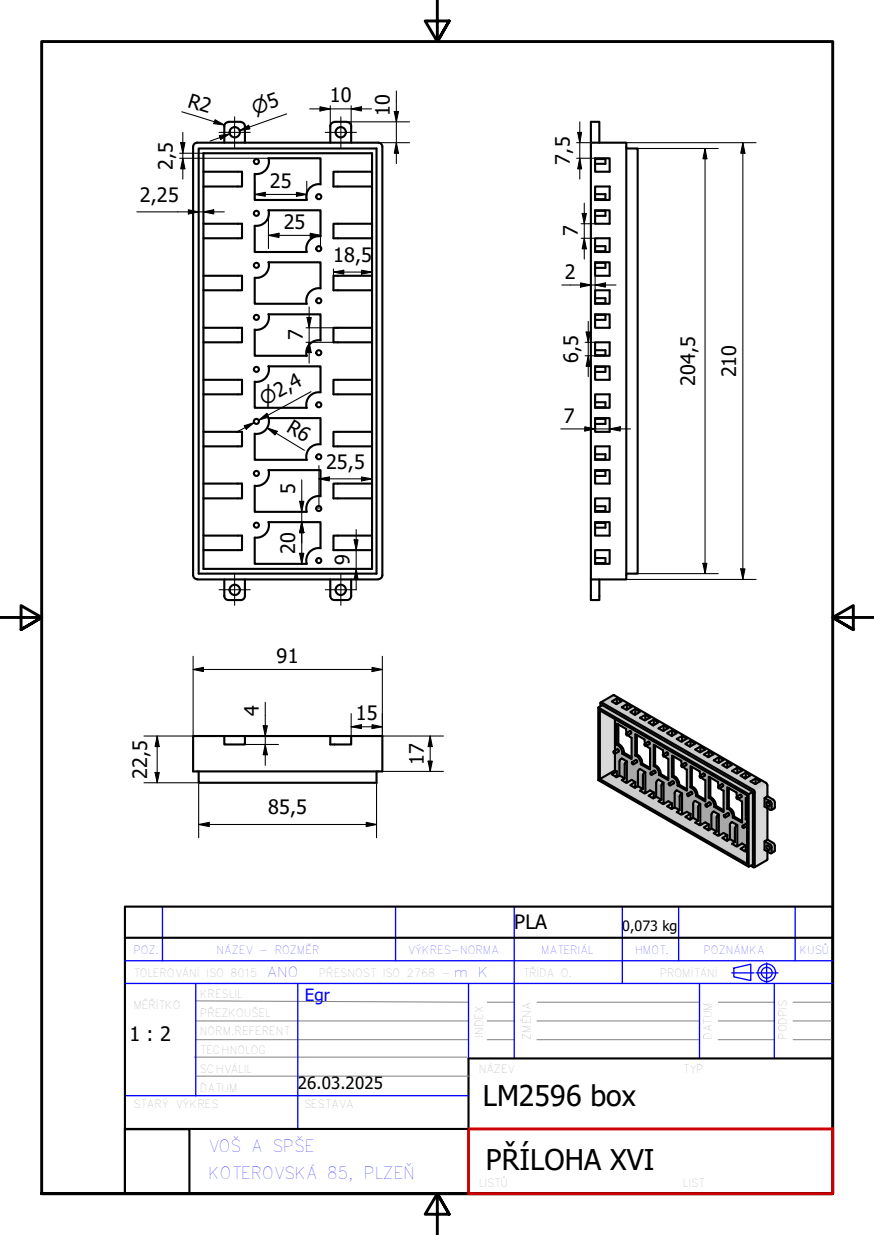
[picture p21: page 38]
VÝKRES-NORMA; POZ.; NÁZEV - ROZMĚR; POZNÁMKA; ZMĚNA; INDEX; MATERIÁL; DATUM; HMOT.; PODPIS; KUSŮ; PLA; PŘÍLOHA XVI

TOLEROVÁNÍ ISO 8015 ANO PŘESNOST ISO 2768 -m K | TŘÍDA O. | PROMÍTÁNÍ

MĚŘÍTKO 1 : 2 | KRESLIL | Egr

PŘEZKOUŠEL

NORM.REFERENT
TECHNOLOG
SCHVÁLIL | | NÁZEV TYP LM2596 box
DATUM | 26.03.2025

STARÝ VÝKRES | | SESTAVA

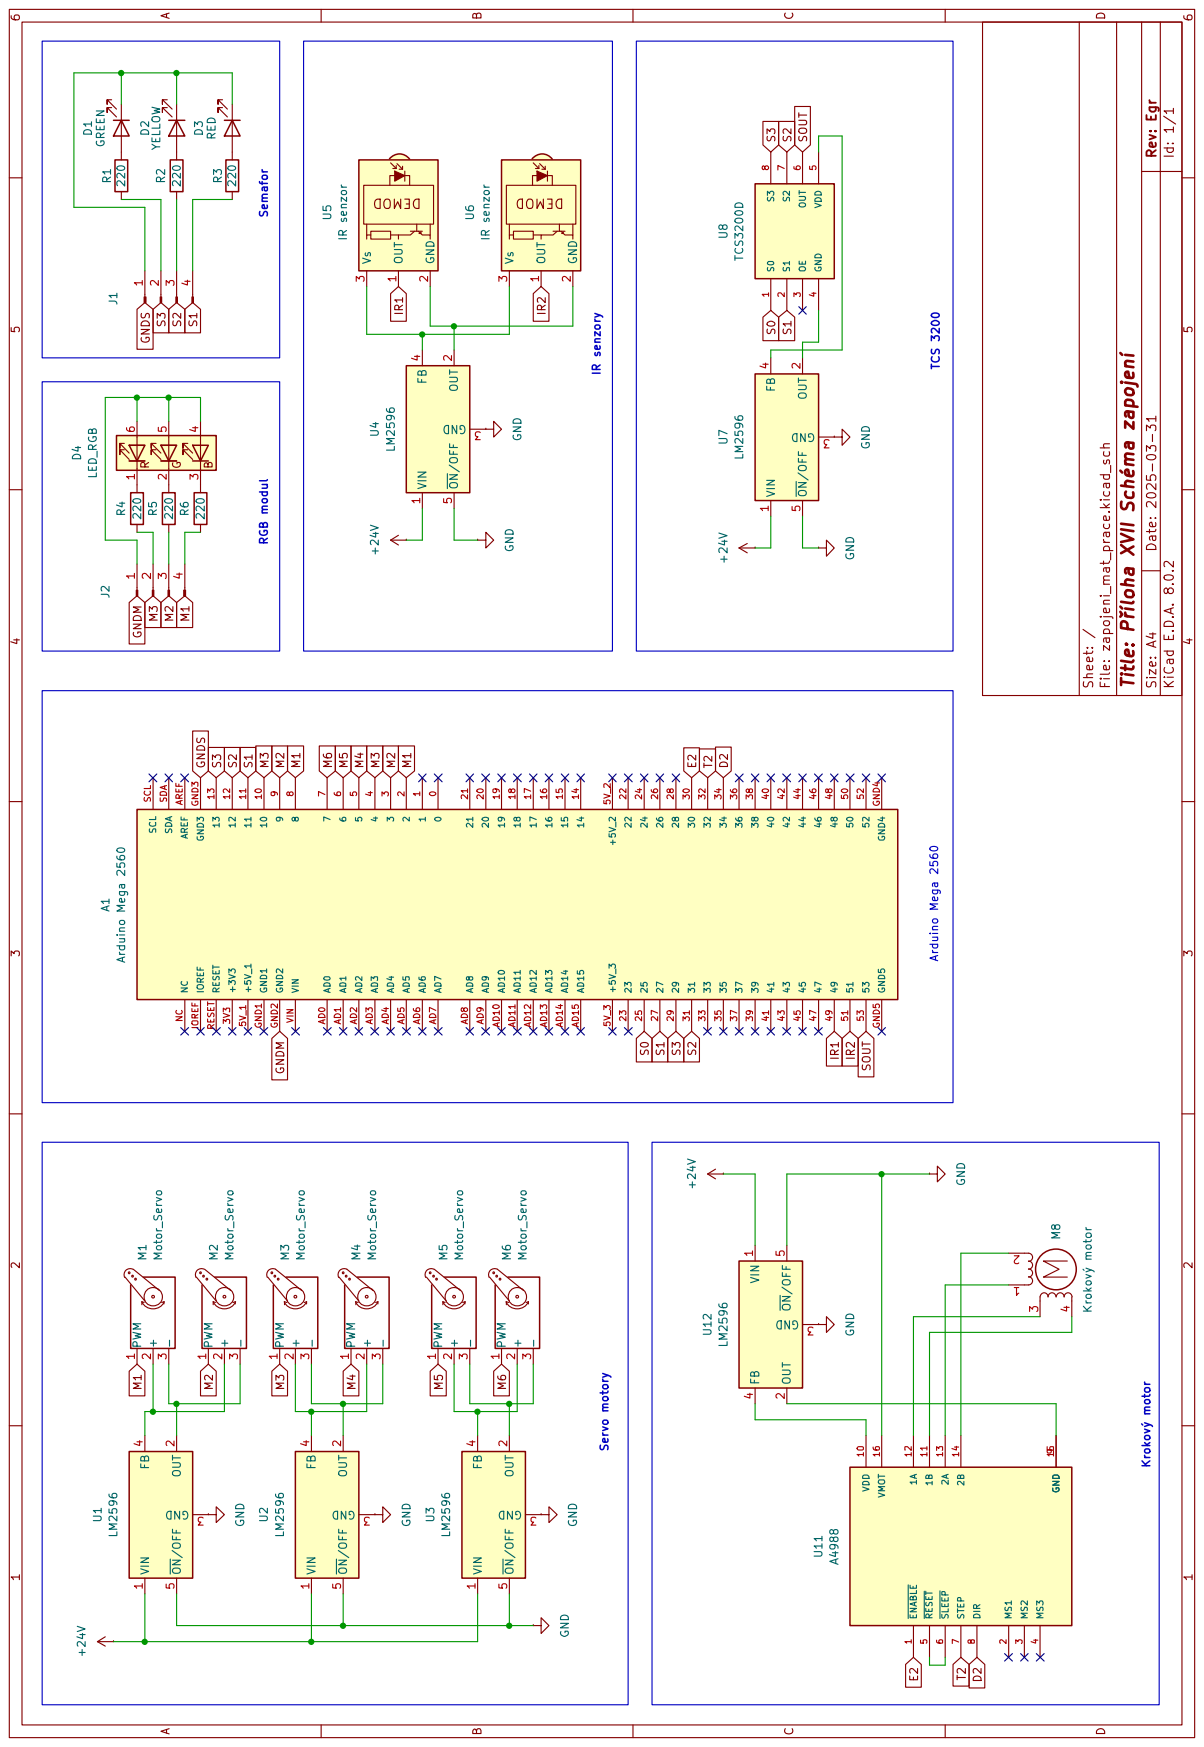
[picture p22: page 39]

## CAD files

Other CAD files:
PROJEKTOVÁ_DATA/3D_modely + vykresy/IR_senzor_hold_v2.idw
PROJEKTOVÁ_DATA/3D_modely + vykresy/IR_senzor_hold_v2.ipt
PROJEKTOVÁ_DATA/3D_modely + vykresy/a4988_box.idw
PROJEKTOVÁ_DATA/3D_modely + vykresy/a4988_box.ipt
PROJEKTOVÁ_DATA/3D_modely + vykresy/a4988_box_lid.idw
PROJEKTOVÁ_DATA/3D_modely + vykresy/a4988_box_lid.ipt
PROJEKTOVÁ_DATA/3D_modely + vykresy/arduino_box.idw
PROJEKTOVÁ_DATA/3D_modely + vykresy/arduino_box.ipt
PROJEKTOVÁ_DATA/3D_modely + vykresy/arduino_lid.idw
PROJEKTOVÁ_DATA/3D_modely + vykresy/arduino_lid.ipt
PROJEKTOVÁ_DATA/3D_modely + vykresy/blet_leg_30x30 - rozsirene (zdcardlove).ipt
PROJEKTOVÁ_DATA/3D_modely + vykresy/blet_leg_30x30 - rozsirene.idw
PROJEKTOVÁ_DATA/3D_modely + vykresy/blet_leg_30x30 - rozsirene.ipt
PROJEKTOVÁ_DATA/3D_modely + vykresy/connector_30x30.ipt
PROJEKTOVÁ_DATA/3D_modely + vykresy/cube.ipt
PROJEKTOVÁ_DATA/3D_modely + vykresy/krouzek.ipt
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

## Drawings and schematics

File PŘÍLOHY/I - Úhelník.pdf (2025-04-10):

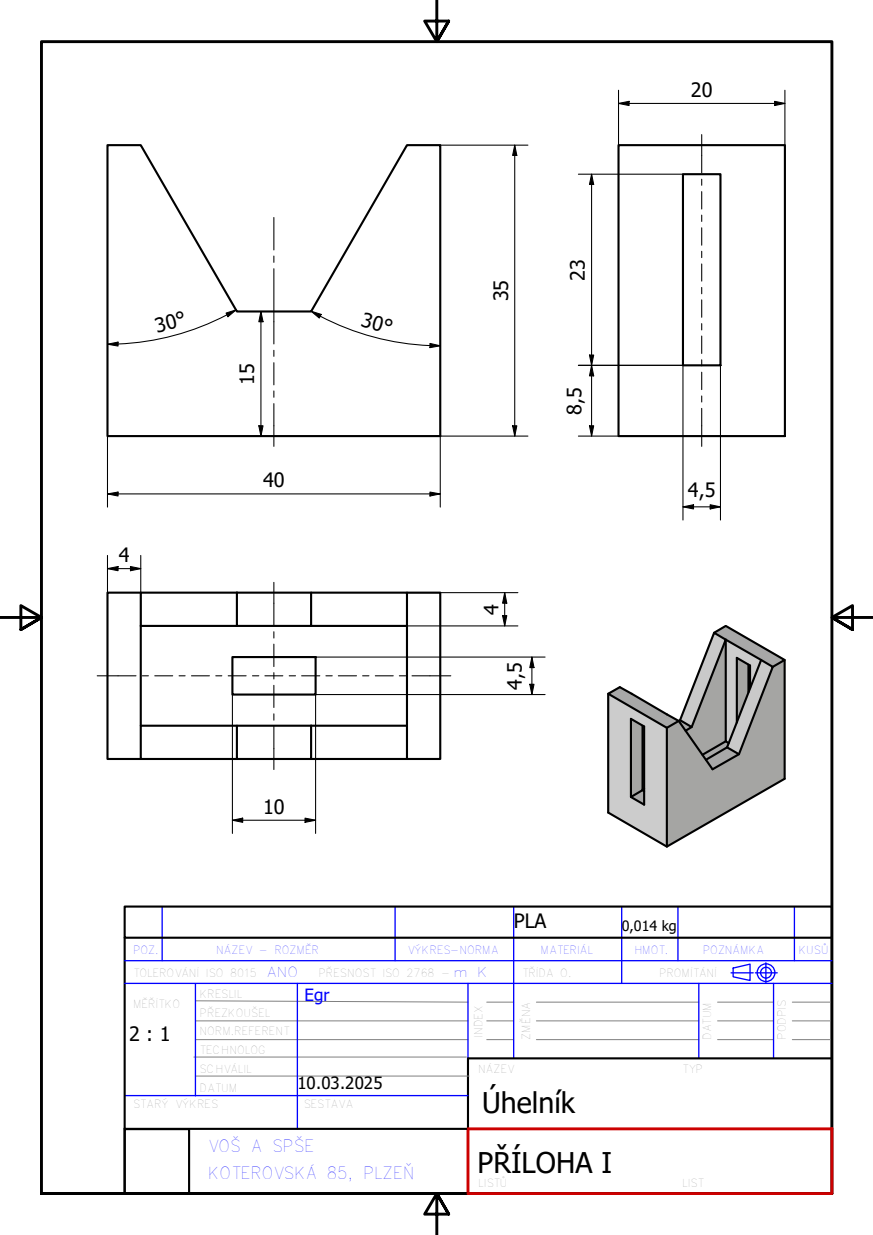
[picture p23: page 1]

PLA | 0,014 kg

POZ. | NÁZEV - ROZMĚR | VÝKRES-NORMA | MATERIÁL | HMOT. | POZNÁMKA | KUSŮ

TOLEROVÁNÍ ISO 8015 ANO PŘESNOST ISO 2768 -m K | TŘÍDA O. | PROMÍTÁNÍ

MĚŘÍTKO 2 : 1 | KRESLIL | Egr

PŘEZKOUŠEL

NORM.REFERENT
TECHNOLOG
SCHVÁLIL | | NÁZEV TYP Úhelník
DATUM | 10.03.2025

STARÝ VÝKRES | | SESTAVA

VOŠ A SPŠE KOTEROVSKÁ 85, PLZEŇ | PŘÍLOHA I LISTŮ LIST

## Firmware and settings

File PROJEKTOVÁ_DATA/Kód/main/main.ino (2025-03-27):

#include <Arduino.h>
#include <Servo.h>

// Definování pinů na TCS3200
#define S0 51 // zeleny
#define S1 53 // zluty
#define S2 49 // fialovy
#define S3 47 // modry
#define Out A15 // sedivy

// Definování IR pinů (IR1 = barva, IR2 = rameno)
#define IR1 36 
#define IR2 38

// Definování NEMA 17 (pas)
#define dirPin 50 //zluty
#define stepPin 52 // oranzovy
#define enablePin 48 // zeleny
const int stepsPerRevolution = 3600;

// Deklarace servomotorů pro rameno (1-6)
Servo osa1;
Servo osa2;
Servo osa3;
Servo osa4;
Servo osa5;
Servo osa6;

// Piny pro připojení servomotorů
#define PIN_OSA1 2
#define PIN_OSA2 3
#define PIN_OSA3 4
#define PIN_OSA4 5
#define PIN_OSA5 6
#define PIN_OSA6 7

// RGB LED modul KY-016
#define pinR 10 // bílý
#define pinG 9 //šedivy
#define pinB 8 // fialový
const int maxSvit = 50;

// semafor
#define cervena_semafor 13 //bílá
#define zluta_semafor 12 //šedivý
#define zelena_semafor 11 //fialová
int pauza = 1000; //nastavíme si jak dlouhou chceme pauzu



// Nastavení globální proměnné pro barvu
String detectedColor = "";

String barva = "";

// Funkce pro debouncing IR senzoru
bool isSensorLowDebounced(int sensorPin, int debounceDelay = 10) {
  if (digitalRead(sensorPin) == LOW) {
    delay(debounceDelay);
    if (digitalRead(sensorPin) == LOW) {
      if (digitalRead(sensorPin) == LOW) {
        delay(debounceDelay);
        if (digitalRead(sensorPin) == LOW) {
          return true;
        }
      }
    }
  }
  return false;
}


void setup() {
  // semafor
  pinMode(cervena_semafor, OUTPUT);
  pinMode(zluta_semafor, OUTPUT);
  pinMode(zelena_semafor, OUTPUT);

  //rgb modul
  pinMode(pinR, OUTPUT);
  pinMode(pinG, OUTPUT);
  pinMode(pinB, OUTPUT);

  // Krokový motor
  pinMode(stepPin, OUTPUT);
  pinMode(dirPin, OUTPUT);
  pinMode(enablePin, OUTPUT);
  digitalWrite(enablePin, LOW); // Aktivace driveru
  
  // Nastavení seriové linky
  Serial.begin(9600);
  
  // TCS3200
  pinMode(S0, OUTPUT);
  pinMode(S1, OUTPUT);
  pinMode(S2, OUTPUT);
  pinMode(S3, OUTPUT);
  pinMode(Out, INPUT);
  digitalWrite(S0, HIGH);
  digitalWrite(S1, LOW);

  // IR senzory
  pinMode(IR1, INPUT);
  pinMode(IR2, INPUT);

  semafor("cervena");

  // Servo inicializace
  delay(2000);
  enableArm();
  delay(1000);
  armReset();

  delay(500);

  startMotorForDuration(3600);
  stopMotor();
  delay(1000);
  semafor("zelena");
}

void loop() {
  semafor("zelena");
  
  // Spustí motor a čeká pouze na aktivaci IR1
  startMotorUntilSensorPin(IR1, 550);
  stopMotor();
  semafor("zluta");


  delay(1000);

  detectedColor = scanColor();
  Serial.println("Detekovaná barva: " + detectedColor);

  if (detectedColor == "R") {
    nastavRGB(maxSvit, 0, 0);
  } else if (detectedColor == "G") {
    nastavRGB(0, maxSvit, 0);
  } else if (detectedColor == "B") {
    nastavRGB(0, 0, maxSvit);
  }

  delay(1000);
  
  // Opět spustí motor a čeká na aktivaci IR1
  startMotorUntilSensorPin(IR2, 900);
  stopMotor();

  if (detectedColor == "R") {
    Serial.println("Cervena kostka");
    enableArm();
    cubeGrab();
    cubeRed();
    armReset();
  } else if (detectedColor == "G") {
    Serial.println("Zelena kostka");
    enableArm();
    cubeGrab();
    cubeGreen();
    armReset();
  } else if (detectedColor == "B") {
    Serial.println("Modra kostka");
    enableArm();
    cubeGrab();
    cubeBlue();
    armReset();
  } else if (detectedColor == "XXX") {
    Serial.println("Neznama kostka");
    enableArm();
    cubeGrab();
    cubeUknown();
    armReset();
  }
  delay(1000);
  nastavRGB(0, 0, 0);
  Serial.println("Cyklus dokončen");

}

// Funkce pro spuštění motoru **dokud nesepne kterýkoliv IR senzor**
void startMotorUntilSensorPin(int sensorPin, int extraSteps) {
  Serial.println("Motor start");
  digitalWrite(enablePin, LOW);
  digitalWrite(dirPin, HIGH); // Směr pohybu

  // Motor běží, dokud zvolený senzor nedetekuje stabilní LOW signál
  while (!isSensorLowDebounced(sensorPin)) {
    digitalWrite(stepPin, HIGH);
    delayMicroseconds(1000);
    digitalWrite(stepPin, LOW);
    delayMicroseconds(1000);
  }
  
  // Po detekci provede definovaný počet extra kroků
  Serial.print("Senzor na pinu ");
  Serial.print(sensorPin);
  Serial.println(" aktivován - pokračuji ještě extra kroky");
  for (int i = 0; i < extraSteps; i++) {
    digitalWrite(stepPin, HIGH);
    delayMicroseconds(1000);
    digitalWrite(stepPin, LOW);
    delayMicroseconds(1000);
  }
  
  // Po provedení extra kroků počká, dokud se senzor neuvolní
  while (digitalRead(sensorPin) == LOW) {
    delay(10);
  }
}

// Funkce pro zastavení motoru
void stopMotor() {
  Serial.println("Motor stop");
  digitalWrite(enablePin, HIGH);
}

void startMotorForDuration(int duration) {
  Serial.println("Motor běží po dobu " + String(duration) + " ms");
  digitalWrite(enablePin, LOW);
  digitalWrite(dirPin, HIGH);

  for (int i = 0; i < duration / 4; i++) {
    digitalWrite(stepPin, HIGH);
    delayMicroseconds(1000);
    digitalWrite(stepPin, LOW);
    delayMicroseconds(1000);
  }

  stopMotor();
  Serial.println("Kostka pryč");
  delay(3000);
}

// Funkce pro detekci barvy
String scanColor() {
  int attempts = 0;

  while (attempts < 5) { // Opakuj měření maximálně 5x
    digitalWrite(S2, LOW);
    digitalWrite(S3, LOW);
    int red = pulseIn(Out, LOW);
    delay(50);

    digitalWrite(S2, HIGH);
    digitalWrite(S3, HIGH);
    int green = pulseIn(Out, LOW);
    delay(50);

    digitalWrite(S2, LOW);
    digitalWrite(S3, HIGH);
    int blue = pulseIn(Out, LOW);
    delay(50);

    Serial.print("R: ");
    Serial.print(red);
    Serial.print(" | G: ");
    Serial.print(green);
    Serial.print(" | B: ");
    Serial.println(blue);

    // Rozhodování o barvě
    if (red < 50) {
      Serial.println("Barva červená");
      return "R";
    } else if (green < 50) {
      Serial.println("Barva zelená");
      return "G";
    } else if (blue < 50) { 
      Serial.println("Barva modrá");
      return "B";
    }

    Serial.println("Barva nerozpoznána, opakuji měření...");
    attempts++;
    delay(500); // Počkej půl sekundy před novým měřením
  }

  Serial.println("Neznámá kostka, vracím XXX");
  return "XXX";
}

void moveArm(int a, int b, int c, int d, int e, int f, int steps = 40) {
  int startPos[6] = {osa1.read(), osa2.read(), osa3.read(), osa4.read(), osa5.read(), osa6.read()};
  int endPos[6] = {a, b, c, d, e, f};
  
  for (int s = 0; s <= steps; s++) {
    float t = (float)s / steps;
    // Smoothstep easing function: cubic interpolation for ease in/out
    float ease = t * t * (3 - 2 * t);
    
    osa1.write(startPos[0] + (endPos[0] - startPos[0]) * ease);
    osa2.write(startPos[1] + (endPos[1] - startPos[1]) * ease);
    osa3.write(startPos[2] + (endPos[2] - startPos[2]) * ease);
    osa4.write(startPos[3] + (endPos[3] - startPos[3]) * ease);
    osa5.write(startPos[4] + (endPos[4] - startPos[4]) * ease);
    osa6.write(startPos[5] + (endPos[5] - startPos[5]) * ease);
    
    delay(20);
  }
}

void disableArm() {
  osa1.detach();
  osa2.detach();
  osa3.detach();
  osa4.detach();
  osa5.detach();
  osa6.detach();
  Serial.println("Rameno vypnuto");
}

void enableArm() {
  // Připojení serv, ale bez pohybu
  osa1.attach(PIN_OSA1);
  osa1.write(85);
  osa2.attach(PIN_OSA2);
  osa2.write(5);
  osa3.attach(PIN_OSA3);
  osa3.write(70);
  osa4.attach(PIN_OSA4);
  osa4.write(170);
  osa5.attach(PIN_OSA5);
  osa5.write(60);
  osa6.attach(PIN_OSA6);
  osa6.write(80);
  Serial.println("Rameno aktivováno");
}

void cubeGrab() {
  moveArm(85, 120, 120, 100, 60, 80); //zvedne se z resetu +
  delay(500);
  moveArm(175, 120, 120, 100, 60, 25); // otočí se k pásu a otevřeruku *
  delay(500); 
  moveArm(175, 60, 85, 130, 55, 25); // nahne se k pásu -
  delay(500);
  moveArm(175, 60, 85, 130, 55, 57); //chycení kostky -
  delay(500);
  moveArm(175, 120, 120, 100, 60, 57); // oddálí se od pásu * (zavřena s kostkou)
  delay(500);
}


void armReset() {
  moveArm(85, 5, 70, 170, 60, 80);
  delay(200);
  disableArm();
}

void cubeRed() {
  moveArm( 85, 120, 120, 100, 60, 57); //otočí se zpět + (zavřena s kostkou)
  delay(500);
  moveArm(110, 80, 80, 100, 60, 57); // nahnutí nad místo odhozu
  delay(500);
  moveArm(110, 80, 80, 100, 60, 25); // shození
  delay(500);
  moveArm(85, 120, 120, 100, 60, 80); // nahnutí zpátky
  delay(500);
}

void cubeGreen() {
  moveArm( 85, 120, 120, 100, 60, 57); //otočí se zpět + (zavřena s kostkou)
  delay(500);
  moveArm(85, 40, 20, 90, 60, 57); // nahnutí nad místo odhozu
  delay(500);
  moveArm(85, 40, 20, 90, 60, 25); // shození
  delay(500);
  moveArm(85, 120, 120, 100, 60, 80); // nahnutí zpátky
  delay(500);
}

void cubeBlue() {
  moveArm( 85, 120, 120, 100, 60, 57); //otočí se zpět + (zavřena s kostkou)
  delay(500);
  moveArm(55, 80, 80, 100, 60, 57);// nahnutí nad místo odhozu
  delay(500);
  moveArm(55, 80, 80, 100, 60, 25); // shození
  delay(500);
  moveArm(85, 120, 120, 100, 60, 80); // nahnutí zpátky
  delay(500);
}

void cubeUknown() {
  moveArm(175, 140, 130, 90, 60, 57); // nahnutí nad míst odhozu
  delay(500);
  moveArm(175, 140, 130, 90, 60, 25); // shození
  delay(500);
  moveArm(85, 120, 120, 100, 60, 80); // nahnutí zpátky
  delay(500);
}


void semafor(String barva) {
    digitalWrite(cervena_semafor, LOW);
    digitalWrite(zluta_semafor, LOW);
    digitalWrite(zelena_semafor, LOW);
    
    if (barva == "cervena") {
        digitalWrite(cervena_semafor, HIGH);
    } else if (barva == "zluta") {
        digitalWrite(zluta_semafor, HIGH);
    } else if (barva == "zelena") {
        digitalWrite(zelena_semafor, HIGH);
    }
}

void nastavRGB(int cervena, int zelena, int modra) {
  // nastavení všech barev na zvolené intenzity
  analogWrite(pinR, cervena);
  analogWrite(pinG, zelena);
  analogWrite(pinB, modra);
}

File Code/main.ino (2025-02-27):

#include <Servo.h>

// Definování pinů na TCS3200
#define S0 51
#define S1 53
#define S2 49
#define S3 45
#define Out A7

// Definování IR pinů (IR1 = barva, IR2 = rameno)
#define IR1 36 
#define IR2 38

// Definování NEMA 17 (pas)
#define dirPin 50
#define stepPin 52
const int stepsPerRevolution = 3600;

// Deklarace servomotorů pro rameno (1-6)
Servo osa1;
Servo osa2;
Servo osa3;
Servo osa4;
Servo osa5;
Servo osa6;

// Piny pro připojení servomotorů
#define PIN_OSA1 2
#define PIN_OSA2 3
#define PIN_OSA3 4
#define PIN_OSA4 5
#define PIN_OSA5 6
#define PIN_OSA6 7

// Nastavení globální proměnné pro barvu
String detectedColor = "";

void setup() {
  // Nastavení seriové linky
  Serial.begin(9600);
  
  // TCS3200
  pinMode(S0, OUTPUT);
  pinMode(S1, OUTPUT);
  pinMode(S2, OUTPUT);
  pinMode(S3, OUTPUT);
  pinMode(Out, INPUT);
  digitalWrite(S0, HIGH);
  digitalWrite(S1, LOW);

  // IR senzory
  pinMode(IR1, INPUT);
  pinMode(IR2, INPUT);

  // Krokový motor
  pinMode(stepPin, OUTPUT);
  pinMode(dirPin, OUTPUT);

  // Servo inicializace
  osa1.attach(PIN_OSA1);
  osa2.attach(PIN_OSA2);
  osa3.attach(PIN_OSA3);
  osa4.attach(PIN_OSA4);
  osa5.attach(PIN_OSA5);
  osa6.attach(PIN_OSA6);

  armSetup(); //Uhel 90 všechny
  armReset(); // Uhel kdy bude rameno sedět 
}

void loop() {
  startMotor();

  if (digitalRead(IR1) == HIGH) {
    delay(1000); // Nechá dojet kostku pod TCS (vyzkoušet a opravit)
    stopMotor();
    delay(500);

    detectedColor = scanColor();
    Serial.println("Detecovaná barva: " + detectedColor);

    startMotor();
  }

  if (digitalRead(IR2) == HIGH) {
    delay(1000);
    stopMotor();
    delay(500);

    Serial.println("Rameno aktivováno");
    cubeGrab();

    if (detectedColor == "R") {
      cubeRed(); // Pozice s červenou
    } else if (detectedColor == "G") {
      cubeGreen(); // Pozice se zelenou
    } else if (detectedColor == "B") {
      cubeBlue(); // Pozice s modrou
    }
    
    armReset(); // Base poloha pro rameno
    delay(2000);
  }
}

// Funkce pro spuštění motoru
void startMotor() {
  Serial.println("Motor start");
  digitalWrite(dirPin, HIGH); // Směr pohybu (high = po směru, LOW = proti směru)
  for (int x = 0; x < stepsPerRevolution; x++) {
    digitalWrite(stepPin, HIGH);
    delayMicroseconds(1000); // Nastavení rychlosti pohybu
    digitalWrite(stepPin, LOW);
    delayMicroseconds(1000); // Nastavení rychlosti pohybu
  }
}

// Funkce pro zastavení motoru
void stopMotor() {
  Serial.println("Motor stop");
  digitalWrite(stepPin, LOW); // LOW = neposíláme impulzy
  digitalWrite(dirPin, LOW);  // Vypneme směr, což často zastaví driver
}

// Funkce pro detekci barvy
String scanColor() {
  while (true) { // Opakuj měření, dokud nenajdeme platnou barvu
    digitalWrite(S2, LOW);
    digitalWrite(S3, LOW);
    int red = pulseIn(Out, LOW);
    delay(50);

    digitalWrite(S2, HIGH);
    digitalWrite(S3, HIGH);
    int green = pulseIn(Out, LOW);
    delay(50);

    digitalWrite(S2, LOW);
    digitalWrite(S3, HIGH);
    int blue = pulseIn(Out, LOW);
    delay(50);

    Serial.print("R: ");
    Serial.print(red);
    Serial.print(" | G: ");
    Serial.print(green);
    Serial.print(" | B: ");
    Serial.println(blue);

    // Rozhodování o barvě
    if (red < 60) {
      Serial.println("Barva červená");
      return "R";

    } else if (red >= 190 && red <= 220 &&
               green >= 140 && green <= 160 &&
               blue >= 150 && blue <= 170) {
      Serial.println("Barva zelená");
      return "G";

    } else if (blue > green && blue > red) { 
      Serial.println("Barva modrá");
      return "B";
    }

    Serial.println("Barva nerozpoznána, opakuji měření...");
    delay(500); // Počkej půl sekundy před novým měřením
  }
}


void moveArm(int a, int b, int c, int d, int e, int f) {
  osa1.write(a);
  osa2.write(b);
  osa3.write(c);
  osa4.write(d);
  osa5.write(e);
  osa6.write(f);
  delay(200);
}

void cubeGrab() {
  moveArm(90, 120, 150, 90, 60, 45); //Nadefinovat pozice
}

void cubeRed() {
  moveArm(125, 125, 135, 105, 75, 25); //Nadefinovat pozice
}

void cubeGreen() {
  moveArm(155, 135, 125, 115, 85, 20); //Nadefinovat pozice
}

void cubeBlue() {
  moveArm(185, 145, 115, 125, 95, 15); //Nadefinovat pozice
}

void armReset() {
  moveArm(90, 90, 90, 90, 90, 90); //Nadefinovat pozice
}

void armStup() {
  moveArm(90, 90, 90, 90, 90, 90); //Nadefinovat pozice
}
